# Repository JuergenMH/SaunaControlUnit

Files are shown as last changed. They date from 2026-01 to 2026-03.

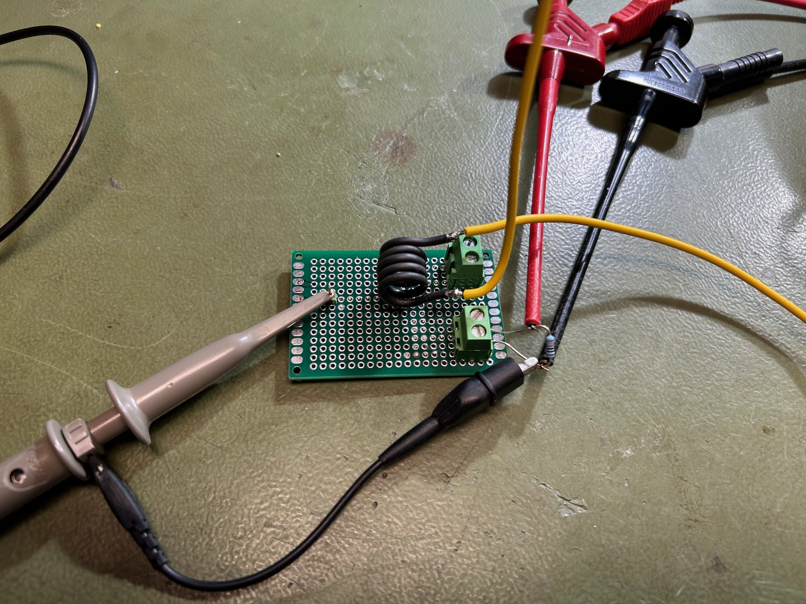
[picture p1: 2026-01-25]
Components/Home brew current sensor/Fotos/6. Coil #3 (in pperation).jpeg

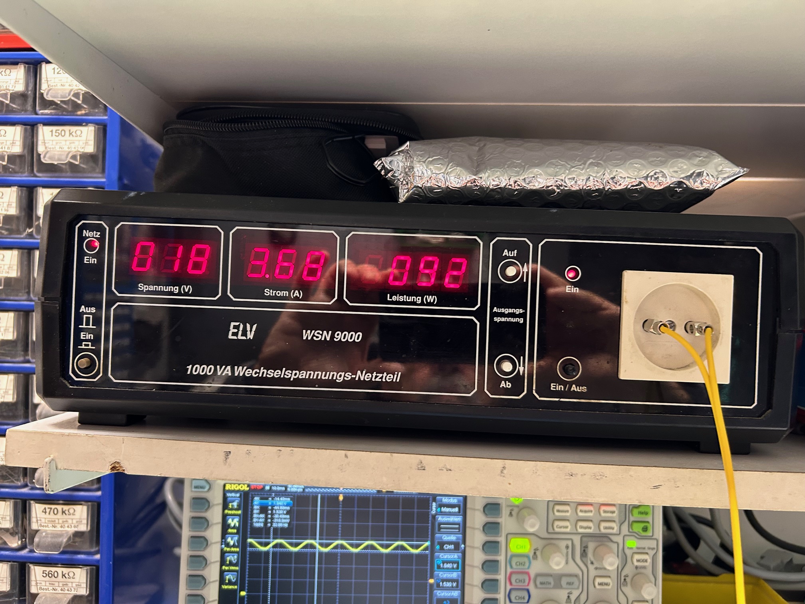
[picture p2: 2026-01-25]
Components/Home brew current sensor/Fotos/2. Power Supply Load Current (10, 20, .. 40V AC).jpeg

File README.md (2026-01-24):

# SaunaControlUnit
Control unit for sauna oven. Ensures comfort and safety.
Cheap control units are good for regualation and some basic safetey functions.
This project is designed to add some comfort and safety topics
- Enhanced safety by control internal power lines and oven function
- Enhanced comfort: Acceess via WLAN
- Two relay banks to ensure the system in case of one relay fails

Folders:
Components: Datasheets and information hardware component related
Documents:  Planning Documents
SaunaPCB:   KiCAD folder for schematic and PCB design files
Simulation: Folder for LTSpice simulation fils
Firmware:   Planned for firmware files, currently empty

Sorry, some documents are available in German only ;-)

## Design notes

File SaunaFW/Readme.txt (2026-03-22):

SW implementation startet with a home-brew cooperative multitasking.
This works fine, but some parts of the SW (e.g. LCD routines) are fare away from beeing "cooperative".
The latest version is stored in the zip file; still not fully implemented!

So I started a different concept. 
The idea is to use the already running FreeRTOS of the ESP32 module board to change the complete SW from cooperative to preemptive scheduling.
I start with an almost empty project and step by step I will move the already coded functions to the preemptive task scheduling.

Current state is:

FreeRTOS-Tasks
- TskMyIODrive.ino; Input driver modle is running and tested. 
- TskMyKTY.ino;     KTY module is running, results are wrong! => DEBUGGING required
- TskMyRelays.ino;  Relay control module, under construction

Other modules
- MyConfig.ino;     Configuration module as a standard arduino function (carry over from last version)
- MyEncoder.ino;    Encoder module ist running; completely interrupt driven; no FreeRTOS task!

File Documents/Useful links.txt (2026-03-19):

Basic information reagarding FreeRTOS and ESP32 (German):
https://wolles-elektronikkiste.de/freertos-mit-esp32-und-arduino-nutzen

Official FreeRTOS Documentaton:
https://www.freertos.org/Documentation/02-Kernel/04-API-references/01-Task-creation/00-TaskHandle

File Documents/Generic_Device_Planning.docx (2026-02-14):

# Bedienelemente

## Taster/Schalter

Netzschalter = > Ein- und Ausschalten der Steuerung („An“ oder „Aus“)

Modus-Taster => Wechsel zwischen den Betriebsarten „Aktiv“, „Standby“ und „Regelung an“
Kurzes Drücken = Wechsel zwischen „Aktiv“ und „Standby“
Langes Drücken = Wechsel zwischen „Aktiv“ und „Regelung an“
Kurzes Drücken im Modus „Regelung an“ = Quittierung Totmannschaltung

Licht-Taster => Licht ein- und ausschalten
Taster geht an Controller; Licht wird über Relais geschaltet
Bei jedem Drücken wechselt der Modus zwischen an und aus.

Drehencoder => Einstellen der Temperatur
Drücken des Tasters = Speichern als neue Default-Temperatur

Nur der Netzschalter schaltet 230V/AC, alle anderen Bedienelemente arbeiten mit Kleinspannung und gehen zur Elektronik.

## Leuchtdioden

Power LED (Grün) => Leuchtet, wenn Netzschalter in Position “An” ist.

Restliche Anzeigen gehen über das Display

## Anzeige (LCD 4 * 20)

Ausführung als hintergrundbeleuchtetes LCD mit Standard-Controller.

Benutzerdefinierte Symbole

- W = WLAN-Symbol
- °C
- Heizsymbol für Heizung an.

Es wird eine Version mit i²C => LCD Konverter verwendet.
Dazu benötigen wir nur 2 CPU-Leitungen.

## Grobkonzept Anzeigen

… ohne Anspruch auf Vollständigkeit

### Betriebsmodus „Aktiv“, warte auf Start (= Long press „Mode“)

1 | 4 | . | 0 | 2 | . | 2 | 0 | 2 | 6 | | 1 | 6 | : | 4 | 0
R | O | O | M | | : | 1 | 8 | °C | | | L | I | G | H | T | : | O | F | F
S | A | U | N | A | : | 7 | 8 | °C | | | D | O | O | R | | : | O | K
T | A | R | G | . | : | 8 | 0 | °C | | | S | T | A | T | E | : | R | D | Y

### Betriebsmodus „Regelung“

1 | 4 | . | 0 | 2 | . | 2 | 0 | 2 | 6 | | 1 | 6 | : | 4 | 0
R | O | O | M | | : | 1 | 8 | °C | | | L | I | G | H | T | : | O | F | F
S | A | U | N | A | : | 7 | 8 | °C | | | D | O | O | R | | : | O | K
T | A | R | G | . | : | 8 | 0 | °C | | | S | T | A | T | E | : | O | N | | Of

Of = Heizsymbol, wenn gerade geheizt wird.
Idee: Der Status blinkt, um den Betrieb etwas deutlicher anzuzeigen.

### Fehler: Tür offen

Wenn bei offener Tür versucht wird die Regelung zu starten:

1 | 4 | . | 0 | 2 | . | 2 | 0 | 2 | 6 | | 1 | 6 | : | 4 | 0
R | O | O | M | | : | 1 | 8 | °C | | | L | I | G | H | T | : | O | F | F
S | A | U | N | A | : | 7 | 8 | °C | | | D | O | O | R | | : | O | K
T | A | R | G | . | : | 8 | 0 | °C | | | S | T | A | T | E | : | D | O | O | R

Summe ertönt, Fehler wird für 2 Sekunden angezeigt, dann geht es zurück zum Zustand „Aktiv“

### Fehler: Übertemperatursicherung ausgelöst

1 | 4 | . | 0 | 2 | . | 2 | 0 | 2 | 6 | | 1 | 6 | : | 4 | 0
R | O | O | M | | : | 1 | 8 | °C | | | L | I | G | H | T | : | O | F | F
S | A | U | N | A | : | 7 | 8 | °C | | | D | O | O | R | | : | O | K
E | R | R | O | R | : | O | V | E | R | T | E | M | P | R | A | T | U | R | E

Summer ertönt, Regelung kann nicht mit Mode gestartet werden.

### Fehler: Sensorfehler Sauna

1 | 4 | . | 0 | 2 | . | 2 | 0 | 2 | 6 | | 1 | 6 | : | 4 | 0
R | O | O | M | | : | 1 | 8 | °C | | | L | I | G | H | T | : | O | F | F
S | A | U | N | A | : | ? | ? | °C | | | D | O | O | R | | : | O | K
E | R | R | O | R | : | S | E | N | S | O | R | | D | E | F | E | C | T

Summer ertönt, Regelung kann nicht mit Mode gestartet werden.

### Fehler: Sensorfehler Raumtemperatur

1 | 4 | . | 0 | 2 | . | 2 | 0 | 2 | 6 | | 1 | 6 | : | 4 | 0
R | O | O | M | | : | ? | ? | °C | | | L | I | G | H | T | : | O | F | F
S | A | U | N | A | : | 7 | 8 | °C | | | D | O | O | R | | : | O | K
T | A | R | G | . | : | 8 | 0 | °C | | | S | T | A | T | E | : | O | N | | Of

Summer ertönt kurz, Regelung kann aber gestartet werden. Fehleranzeige über ?? bei der Temperatur.

## Summer

Der Summer gibt ein kurzes Feedback in nachfolgenden Situationen:

- Speichern der eingestellten Temperatur (Drücken des Dreh-Encoders)
- Starten der Ofen-Regelung (Langes Drücken von „Mode“) Stoppen der Ofen-Regelung (Langes Drücken von „Mode“)
- Quittierung der „Totmannschaltung“ (Kurzes Drücken von Mode)

Ein langes Fehlersignal wird dann ausgegeben:

- Regelung soll gestartet werden, während die Tür offen ist
- Regelung soll gestartet werden, während ein Fehler vorliegt. (z.B. Überhitzungsschutz hat ausgelöst, sonstiger HW-Fehler)

# Powermodi

Netzschalter in Position „Aus“ => „Power off“, Elektronik inaktiv

Netzschalter in Position „An“ => „Power on“, Elektronik aktiv

Betriebsmodus „Standby“ => Alle Anzeigen aus, WLAN ist aktiv

Betriebsmodus „Aktiv“ => Display an, Regelung kann gestartet werden

Betriebsmodus „Regelung“ => Display an, Regelung wurde gestartet

Nach dem Einschalten des Netzschalters geht das System in den Zustand „An“ + „Aktiv“

Durch kurzes Drücken des Mode-Tasters wird zwischen „Aktiv“ und „Standby“ gewechselt.
Durch langes Drücken des Mode-Tasters wird die Regelung gestartet.

# Lichtsteuerung

Hinweis: Im Modus „Power off“ kann das Licht nicht eingeschaltet werden.
Um das Licht aktivieren zu können, muss das System im Modus „Power On“ sein.

Unabhängig vom Betriebsmodus (Aktiv/Standby) kann das Licht durch Druck auf den Licht-Taster ein- oder ausgeschaltet werden.

Wird die Regelung über den Start-Taster aktiviert, wird automatisch das Licht eingeschaltet.

# Grundlegende Bedienung im Saunabetrieb

## Allgemeine Nutzung

Sollte der Netzschalter in der Position „Aus“ stehen, ist der Schalter zuerst in die Position „An“ zu stellen. In diesem Fall wird nach dem Einschalten direkt der Betriebsmodus „Aktiv“ gewählt.

Ist der Netzschalter in der Position „An“ und der Betriebsmodus ist „Standby“, wird nach dem Drücken auf die Mode-Taster in den Modus „Aktiv“ gewechselt.

Anzeigt werden nun auf dem LCD:

- Status WLAN Verbindung (WLAN-SYMBOL)
- Uhrzeit (NTP, für spätere Erweiterungen)
- Aktuelle Temperatur in der Sauna und im Raum
- Zieltemperatur

Die Zieltemperatur ist die letzte eingestellte und gespeicherte Temperatur.
Sie kann über den Drehregler in den Grenzen von 40 bis 99°C eingestellt werden. Durch Drücken auf den Encoder-Knopf wird sie als nächste Default-Temperatur gespeichert.

Die Sauna heizt auf, nachdem der Mode-Knopf lange (3 Sekunden) gedrückt wurde.

Um die Ofenreglung abzuschalten, muss der Mode-Knopf wieder lange (3 Sekunden) gedrückt werden.
Hinweis: Kurzes Drücken des Mode-Knopfes setzt nur den Sicherheitstimer #1 zurück. Siehe dazu Kapitel „Sicherheitsfunktionen“.

Während des Betriebes kann jederzeit die Zieltemperatur verändert und auf Wunsch durch Drücken des Encoder-Knopfes auch gespeichert werden.

## Energie sparen (Software Funktionen)

1. Sollte das Gerät für mehr als drei Stunden aktiv sein, ohne dass der Regler gestartet wurde, schaltet das System automatisch in den Betriebsmodus „Standby“ zurück.
2. Wird zwei Stunden nach dem Drücken des Start-Tasters (Aufheizen) nicht die Saunatür geöffnet oder die Start-Taste am Regler gedrückt, wird die Ofenregelung wieder abgeschaltet.

Anmerkung: Die gesetzliche Regelung von max. 6 Stunden kommt nicht zur Anwendung, da die zweite Abschaltfunktion das weitestgehend mit abdeckt.

# Sicherheitsfunktionen

Das System weist mehrere Sicherheitsfunktionen auf:

1. Doppel-Relais (Hardware) Zwei in Reihe geschaltete Relais sollen sicherstellen, dass beim Kleben eines Relaiskontaktes keine Spannung dauerhaft am Ofen anliegt. Relais #1 schaltet, sobald die Ofenregelung gestartet wurde, dauerhaft an. Relais #2 realisiert dann die Regelung.
2. Übertemperaturabschaltung (Hardware) Wenn die Übertemperatursicherung anspricht, bekommen beide Relais keine Versorgungsspannung mehr und können nicht mehr aktiviert werden. Die Spannung wird von der Steuerung überwacht und es wird ein entsprechender Fehler ausgegeben. Ein Betrieb ist nicht möglich! Fehler zurücksetzen: Gerät reparieren und vollständigen Power-Zyklus
3. Sensorüberwachung Im Fall eines Kurzschlusses oder einer Unterbrechung der Sensorleitung wird ein entsprechender Fehler ausgegeben. Ein Betrieb der Steuerung ist dann nicht möglich. Fehler zurücksetzen: Sensor / Kabel reparieren und vollständigen Power-Zyklus
4. Tür-Schalter (Hardware) Die Ofenregelung kann nur bei geschlossener Saunatür gestartet werden. Wird versucht die Ofenregelung bei offener Tür zu starten, gibt es ein Signal vom Summer und es wird eine entsprechende Fehlermeldung ausgegeben. Fehler zurücksetzen: Tür schließen
5. Sicherheitstimer #1 (Software, Totmannschaltung) Ein 20-Minuten-Sicherheitstimer wird aktiviert, wenn die Temperatur mindestens 80% der Zieltemperatur erreicht hat und die Tür geöffnet wird. Danach wird der Sicherheitstimer bei jedem Öffnen der Tür zurückgesetzt und neu gestartet. Durch Drücken des Start-Tasters kann der Sicherheitstimer zusätzlich manuell zurückgesetzt werden. Das Zurücksetzen wird durch einen kurzen Signalton quittiert. Läuft der Timer ohne Quittierung ab, wird die Ofenregelung abgeschaltet, ein langer Signalton ausgegeben und eine Fehlermeldung angezeigt. Fehler zurücksetzen: Start Taster drücken
6. Sicherheitstimer #2 (Software, Saunabetrieb; gesetzliche Regelung) Nach sechs Stunden Saunabetrieb bei aktiver Ofenregelung wird diese automatisch abgeschaltet. Zusätzlich wird ein langer Signalton ausgegeben und eine Fehlermeldung angezeigt. Fehler zurücksetzen: System in den Betriebsmodus „Standby“ schalten

Ende des Dokuments

Konzept Saunasteuerung

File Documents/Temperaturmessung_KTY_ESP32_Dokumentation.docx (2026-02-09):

Temperaturmessung mit KTY-Sensor und ESP32

Technische Dokumentation

Autor: Juergen Eggeling
Datum: 09.02.2026

# Inhaltsverzeichnis

Hinweis: Das Inhaltsverzeichnis kann in Word über „Feld aktualisieren“ automatisch erzeugt werden.

# 1 Einleitung

Dieses Dokument beschreibt die Auslegung, Berechnung und Implementierung einer präzisen Temperaturmessung mit einem KTY-Temperatursensor (2000 Ω @ 25°C) an einem ESP32 unter Verwendung der Arduino-IDE.

# 2 Hardwareaufbau

Der KTY-Sensor ist zwischen ADC-Eingang und Masse geschaltet. Ein Pull-Up-Widerstand verbindet den ADC-Eingang mit der 3,3-Versorgung.

# 3 Blockschaltbild

+3.3V
|
[Pull-Up 2kΩ]
|
[ADC ESP32]
|
[KTY Sensor 2kΩ @25°C]
|
GND

# 4 Messprinzip

Der KTY-Sensor bildet mit dem Pull-Up-Widerstand einen Spannungsteiler. Die am ADC gemessene Spannung wird digitalisiert und anschließend in einen Sensorwiderstand umgerechnet.

# 5 Mathematisches Modell

Die Umrechnung von Widerstand in Temperatur erfolgt über ein kubisches Polynom nach der KTY-Normkennlinie. Die Inversion erfolgt mittels Newton-Iteration.

# 6 Kalibrieranleitung (1-Punkt)

1. Sensor und Referenzthermometer auf gleiche Temperatur bringen (z. B. 25°C).
2. Temperaturwert des ESP32 auslesen (T_mess).
3. Offset berechnen: T_OFFSET = T_ref – T_mess.
4. Offset im Code als Konstante eintragen oder im EEPROM speichern.
5. Offset bei jeder Messung addieren.

# 7 Fehlerbetrachtung

Ohne Kalibrierung ist mit einem typischen Gesamtfehler von ±0,8 bis ±1,2°C zu rechnen. Mit einer 1-Punkt-Kalibrierung reduziert sich der Fehler auf etwa ±0,4°C.

# 8 Optimierung des Pull-Up-Widerstands

Für den Messbereich 20–100°C ist ein Pull-Up-Widerstand von 2,2 kΩ bis 2,49 kΩ optimal, da er den Arbeitspunkt des Spannungsteilers in den linearen ADC-Bereich legt.

# 9 Arduino-Code

const int adcPin = 34;
const float Vref = 3.3;
const float pullup = 2000.0;
const float R25 = 2000.0;
const float A = 7.88e-3;
const float B = 1.94e-5;
const float C = 3.42e-8;
const float T_OFFSET = 0.0; // Kalibrierwert

float R_from_T(float T) {
float x = T - 25.0;
return R25 * (1 + A*x + B*x*x + C*x*x*x);
}

float dR_dT(float T) {
float x = T - 25.0;
return R25 * (A + 2*B*x + 3*C*x*x);
}

float T_from_R(float R) {
float T = 60.0;
for (int i = 0; i < 4; i++) {
T -= (R_from_T(T) - R) / dR_dT(T);
}
return T + T_OFFSET;
}

void setup() {
Serial.begin(115200);
analogReadResolution(12);
analogSetAttenuation(ADC_11db);
}

void loop() {
int adc = analogRead(adcPin);
float voltage = adc * (Vref / 4095.0);
float Rkty = pullup * (voltage / (Vref - voltage));
float temperature = T_from_R(Rkty);

Serial.print("Temperatur: ");
Serial.print(temperature, 2);
Serial.println(" °C");
delay(1000);
}

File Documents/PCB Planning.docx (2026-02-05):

# Trace width calculation

## Introduction

From the web:

- Tmax chosen = 80°C (to be checked)

Unfortunately, we have a lot of input parameters:

1. Max Power 6KW (my oven) or 9KW (for some headroom)
2. Trace width (2.x .. 3.x mm. >3mm is hard to route!)
3. Copper thickness (35 or 70µm, price?)

## Power sauna oven with 6KW (35µm)

Current per line: 6KW complete, 2KW per line
Iline (L1, L2, L3) = P / U = 2000/230 = 8,7A
Chosen for calculation 9A

Trace width: 3,0mm@35µm

Caclulator on: https://www.leiton.de/leiton-tools-leiterbahnerwaermung.html

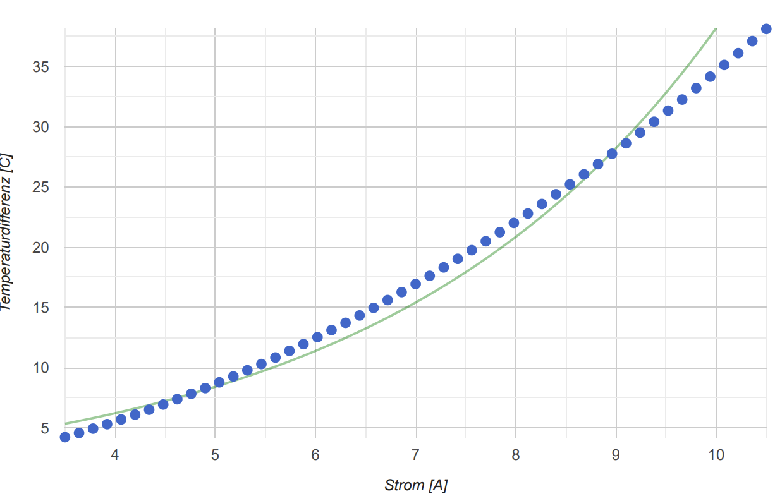
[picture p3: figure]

Delta T expected: + 28°C

Final trace temperature: 22°C room + 28°C heating = 50°C => OK

But 3mm is almost impossible to route under consideration of necessary distances.

## Power sauna oven width 9KW (35µm)

Current per line: 9KW complete, 3KW per line
Iline (L1, L2, L3) = P / U = 3000/230 = 13,04A
Chosen for calculation 13A

Trace width: 3,5mm@35µm

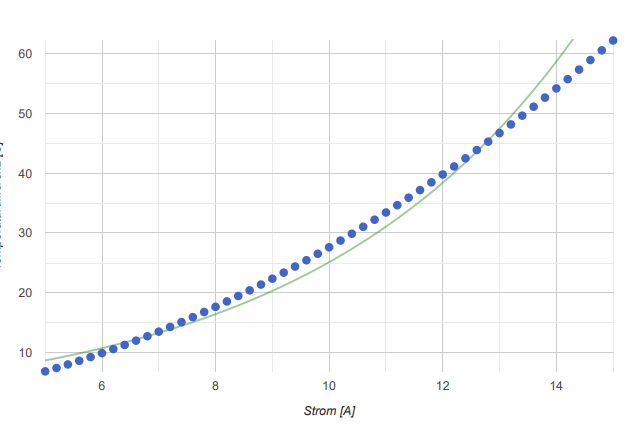
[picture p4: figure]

Delta T expected: + 47°C

Final trace temperature: 22°C room + 28°C heating = 69°C => OK

But 3.5mm is impossible to route under consideration of necessary distances.
=> Lets check 70µm on the next pages.
=> Assume: we try to reduce to 2mm trace width.

## Power sauna oven width 9KW (70µm)

Current per line: 9KW complete, 3KW per line
Iline (L1, L2, L3) = P / U = 3000/230 = 13,04A
Chosen for calculation 13A

Trace width: 2mm@70µm

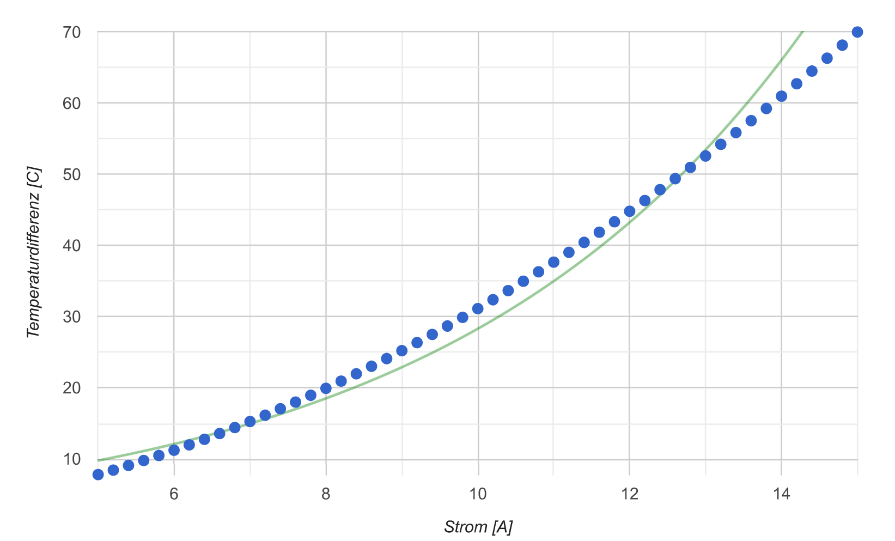
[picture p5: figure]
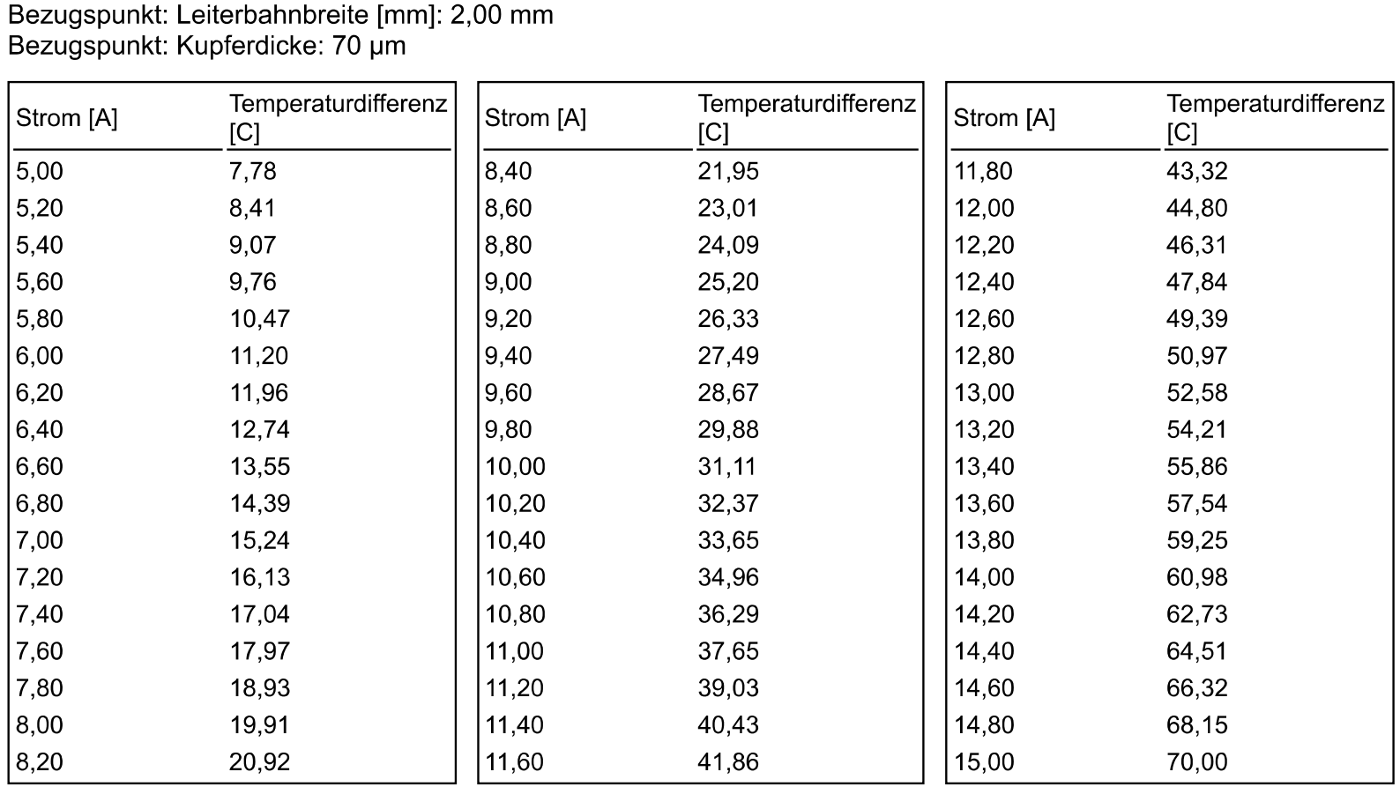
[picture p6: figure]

Delta T expected at 6KW: + 25°C

Final trace temperature: 22°C room + 25°C heating = 47°C => Good

Delta T expected at 9KW: + 53°C

Final trace temperature: 22°C room + 53°C heating = 75°C => Still OK

# Distance calculations

## Legal regulation

From common used legal regulations:

Use case 1: Phase Lx to Lx Functional isolation 2.5mm

Use case 2: Phase Lx to N or PE Base isolation 230V 3.0mm

Use case 3: Phase Lx to Ly Base isolation 400V 4.0mm

Use case 4: Phase Lx to ELV Double / enhanced isolation 6.0mm

With x, y = 1..3, ELV = Extrem low voltage e.g. 24V

## Usage in the design

Use case 1:

- Main switch
- Relay contacts

Use case 2:

- N.a.

Use case 3:

- Between different relays
- Between screw terminals

Use case 4:

- Voltage measurement components (near to Lx)
- Current measurement components (near to Lx)

# Addendum

## Table for temperature rise depending on current and trace width

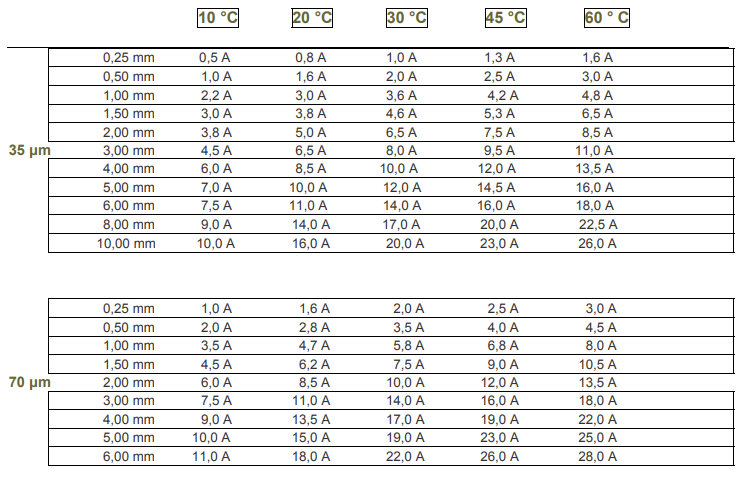
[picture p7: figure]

PCB Planning

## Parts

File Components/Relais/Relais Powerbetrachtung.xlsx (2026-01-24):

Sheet: Relais
Relais |  |  |  | Kontakte |  |  |  | Spule bei Nominalbetrieb (U rated) |  |  |  | Spule im Haltebetrieb |  |  | Worst case Betrachtung
Hersteller | Typ | Lieferant | Preis | max. Strom [A] | max. Spannung [VAC] | Schaltspiele | geschätzte Lebensdauer @ 20 Zyklen/Saunagang | Spannung [VDC] | Widerstand [Ohm] | Leistung [W] | Strom [A] | Spannung [VDC] | Strom [A] | Leistung [W] | Relais #1 [mA] | Relais #2 [mA] | Summe [mA] | Leistung [W]
Schrack/TE | RZ03-1A4-D024 | Reichelt | 1.85 | 16A | 250 | 50000 | 2500 | 24 | 1440 | 0.40 | 0.02 | 20 | 0.01 | 0.28 | 0.04 | 0.05 | 0.09 | 2.22
Omon | G2R-1A-E DC24 | Reichelt | 1.75 | 10A | 250 | 100000 | 5000 | 24 | 1100 | 0.52 | 0.02 | 20 | 0.02 | 0.36 | 0.05 | 0.07 | 0.12 | 2.88
Schrack | RP310024 Nachfolger RT314024 | Lager | 0 | 16A | 250 |  |  | 24 | 1100 | 0.52 | 0.02 | 20 | 0.02 | 0.40 | 0.06 | 0.07 | 0.13 | 3.01

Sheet: Leistungsbetrachtung
 | Spannung [V] | Strom [A] | Leistung [W]
Netzteil Spannung, Strom, Leistung | 24 | 0.23 | 5.52
Verbrauch für sechs Relais | 24 | 0.12 | 2.88
Rest für Schaltregler | 24 | 0.11 | 2.64
Für Elektronik bei 90%Wirkungsgrad | 5 | 0.48 | 2.38
Verbraucher ESP Maximalstrom |  | 0.40 |  | senden, kurzfristig
Verbraucher ESP Nominalstrom |  | 0.18 |  | empfangen, normal
=> Damit überhaupt ein LCD mit Hintergrundbeleuchtung betrieben werden kann, ist eine gute Entkopplung mit starken Elektrolytkondensatoren nötig!
Thema Stromversorgung ESP | https://arduino-hannover.de/2018/07/25/die-tuecken-der-esp32-stromversorgung/
Allgemeines zum ESP | https://wolles-elektronikkiste.de/esp32-mit-arduino-code-programmieren

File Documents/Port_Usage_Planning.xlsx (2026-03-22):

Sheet: Signal view
Signal view
Signal | Funktion | Pegel | Pin Name | Stift reihe | Pin Nummer
I_L1 | Analog input | 1,65V +/-x | ADC1_CH0 | 1 | 3
I_L2 | Analog input | 1,65V +/-x | ADC1_CH3 | 1 | 4
I_L3 | Analog input | 1,65V +/-x | ADC1_CH6 | 1 | 5
24VR Feedback | Analog input | 1,65V +/-x | ADC1_CH7 | 1 | 6
L1_Sense | Digital Input | 0-3,3V | GPIO32 | 1 | 7
L2_Sense | Digital Input | 0-3,3V | GPIO33 | 1 | 8
L3_Sense | Digital Input | 0-3,3V | GPIO25 | 1 | 9
Relais_1 | Digital Output | 0-3,3V | GPIO25 | 1 | 10
Relais_2 | Digital Output | 0-3,3V | GPIO27 | 1 | 11
Relais_3 | Digital Output | 0-3,3V | GPIO14 | 1 | 12
Light on/off button | Digital Input | 0-3,3V | GPIO22 | 1 | 13
Standby/On button | Digital Input | 0-3,3V | GPIO13 | 1 | 15
Door contact | Digital Input | 0-3,3V | GPIO15 | 2 | 17
LCD SCL | I2C Interface | 0-3,3V | GPIO22, SCL | 2 | 3
LCD SDA | I2C Interface | 0-3,3V | GPIO21, SDA | 2 | 6
LCD Backlight | Digital Output | 0-3,3V | GPIO19 | 2 | 8 | reserved
ENC_SWITCH | Digital Input | 0-3,3V | GPIO18 | 2 | 9
ENC_CLK | Digital Input | 0-3,3V | GPIO5 | 2 | 10
ENC_DT | Digital Input | 0-3,3V | GPIO17 | 2 | 11
ENC_VCC | Digital Output | 0-3,3V | GPIO16 | 2 | 12
Buzzer | Digital Output | 0-3,3V | GPIO2 | 2 | 24
KTY oven input | Analog input | 1,65V +/-x | ADC2_CH0 | 2 | 13
KTY room input | Analog input | 1,65V +/-x | ADC2_CH1 | 2 | 14

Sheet: ESP module view
ESP module connector view
Plannig J2 (left row) |  |  |  |  |  | Planning J3 (right row)
No. | Name | Type | Signal | Configuration | Chip function | No. | Name | Type | Signal | Configuration | Chip function
1 | 3V3 | Pwr | N.A. | N.A. | 3.3 V power supply | 1 | GND | Pwr | N.A. | N.A. | Ground
2 | EN | I | N.A. | N.A. | CHIP_PU, Reset | 2 | IO23 | I/O | Buzzer | Digital Output | GPIO23
3 | VP | I | I_L1 | Analog input | GPIO36, ADC1_CH0, S_VP | 3 | IO22 | I/O | LCD SCL | I2C Interface | GPIO22, SCL
4 | VN | I | I_L2 | Analog input | GPIO39, ADC1_CH3, S_VN | 4 | TX | I/O |  |  | GPIO1, U0TXD
5 | IO34 | I | I_L3 | Analog input | GPIO34, ADC1_CH6, VDET_1 | 5 | RX | I/O |  |  | GPIO3, U0RXD
6 | IO35 | I | 24VR Feedback | Analog input | GPIO35, ADC1_CH7, VDET_2 | 6 | IO21 | I/O | LCD SDA | I2C Interface | GPIO21, SDA
7 | IO32 | I/O | L1_Sense | Digital Input | GPIO32, ADC1_CH4, TOUCH_CH9, XTAL_32K_P | 7 | GND | Pwr | N.A. | N.A. | Ground
8 | IO33 | I/O | L2_Sense | Digital Input | GPIO33, ADC1_CH5, TOUCH_CH8, XTAL_32K_N | 8 | IO19 | I/O | Debug | Digital Output | GPIO19
9 | IO25 | I/O | L3_Sense | Digital Input | GPIO25, ADC1_CH8, DAC_1 | 9 | IO18 | I/O | ENC_Switch | Digital Input | GPIO18
10 | IO26 | I/O | Relais_1 | Digital PWM-Output | GPIO26, ADC2_CH9, DAC_2 | 10 | IO5 | I/O | ENC_CLK | Digital Input | GPIO5
11 | IO27 | I/O | Relais_2 | Digital PWM-Output | GPIO27, ADC2_CH7, TOUCH_CH7 | 11 | IO17 | I/O | ENC_DT | Digital Input | GPIO17
12 | IO14 | I/O | Relais_3 | Digital PWM-Output | GPIO14, ADC2_CH6, TOUCH_CH6, MTMS | 12 | IO16 | I/O | ENC_VCC | Digital Output | GPIO16
13 | IO12 | I/O | Light on/ff | Digital Input | GPIO12, ADC2_CH5, TOUCH_CH5, MTDI | 13 | IO4 | I/O | KTY oven input | Analog input | GPIO4, ADC2_CH0, TOUCH_CH0
14 | GND | Pwr | N.A. | N.A. | Ground | 14 | IO0 | I/O |  |  | GPIO0, ADC2_CH1, TOUCH_CH1, Boot
15 | IO13 | I/O | Mode | Digital Input | GPIO13, ADC2_CH4, TOUCH_CH4, MTCK | 16 | IO2 | I/O | KTY room input | Analog input | GPIO2, ADC2_CH2, TOUCH_CH2, !!!)
16 | D2 | I/O | Internally used for communication ESP and flash memory. Do not use! |  |  | 17 | IO15 | I/O | Door contact | Digital Input | GPIO15, ADC2_CH3, TOUCH_CH3, MTDO
17 | D3 | I/O |  |  |  | 17 | D1 | I/O | Internally used for communication ESP and flash memory. Do not use!
18 | CMD | I/O |  |  |  | 18 | D0 | I/O
19 | 5V | Pwr | N.A. | N.A. | 5 V power supply | 19 | CLK | I/O
https://docs.espressif.com/projects/esp-idf/en/v5.1/esp32/hw-reference/esp32/get-started-devkitc.html |  |  |  |  |  | !!!) If KTY not connected (Uin 3,3V) System does not enter Boot mode properly!
https://docs.sunfounder.com/projects/umsk/de/latest/03_esp32/esp32_lesson17_rotary_encoder.html

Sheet: Schematic LCD SPI
e

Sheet: KTY
https://wiki.hshl.de/wiki/index.php/PTC_Temperatursensor_KTY_81-210

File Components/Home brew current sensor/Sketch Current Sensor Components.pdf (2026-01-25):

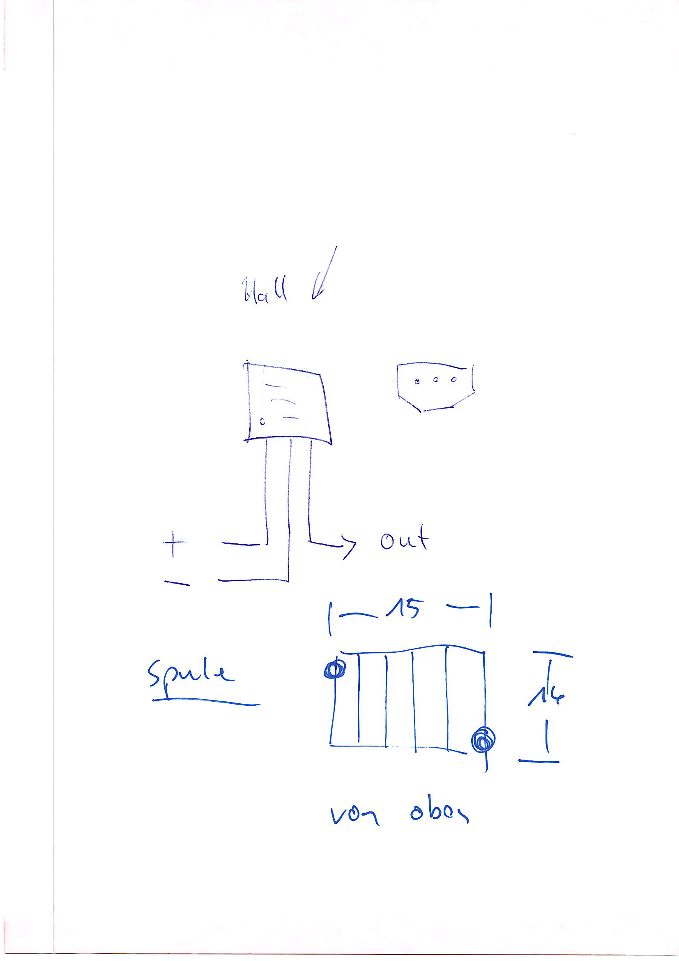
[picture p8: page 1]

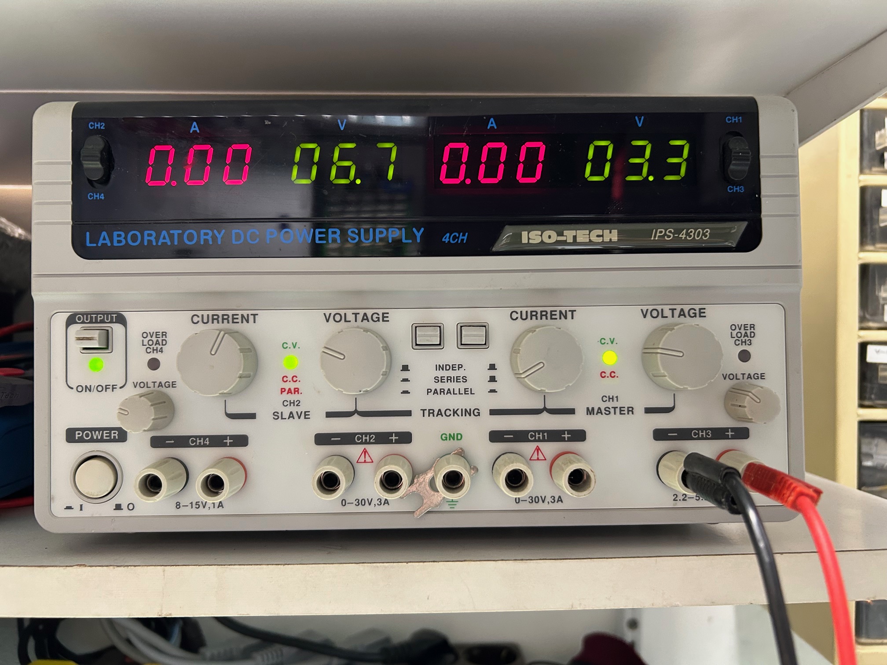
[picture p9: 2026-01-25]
Components/Home brew current sensor/Fotos/1. Power Supply Hall 3,3V.jpeg

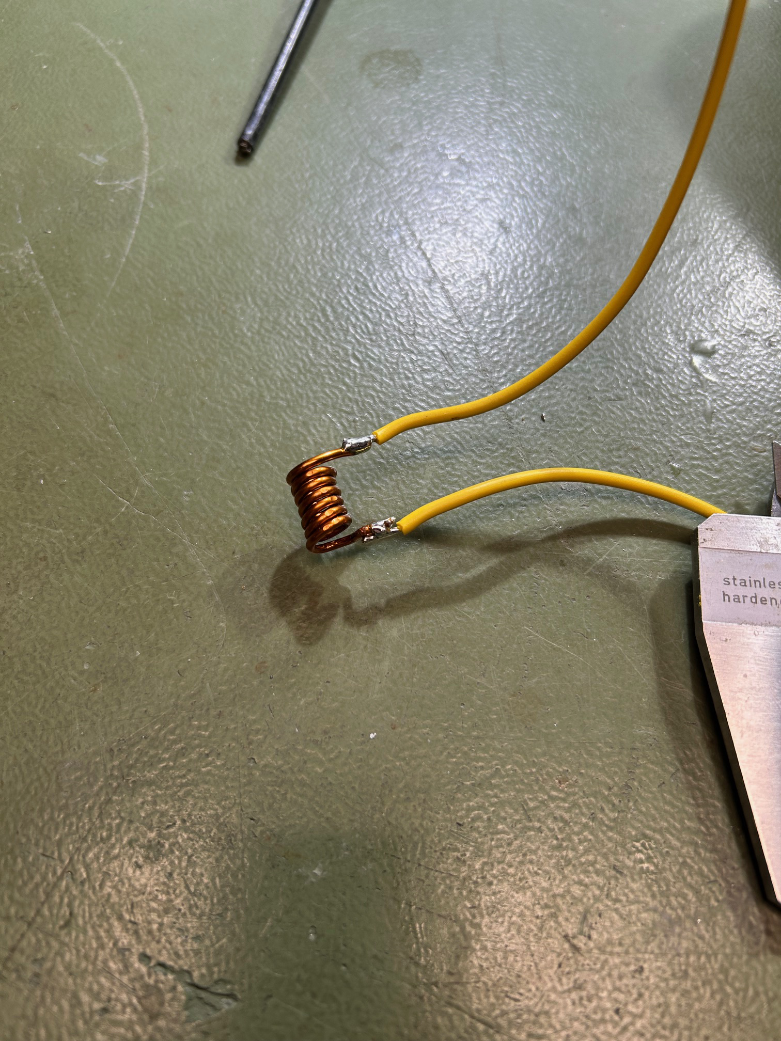
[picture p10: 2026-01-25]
Components/Home brew current sensor/Fotos/5. Coil #2 (on desk).jpeg

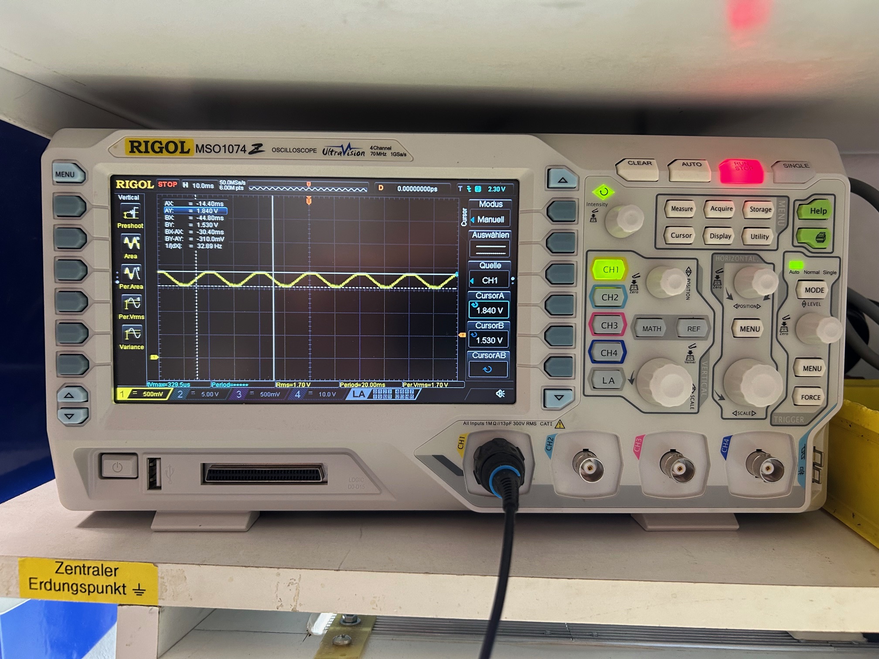
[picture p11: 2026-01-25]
Components/Home brew current sensor/Fotos/4. Hall Voltage Coil #1.jpeg

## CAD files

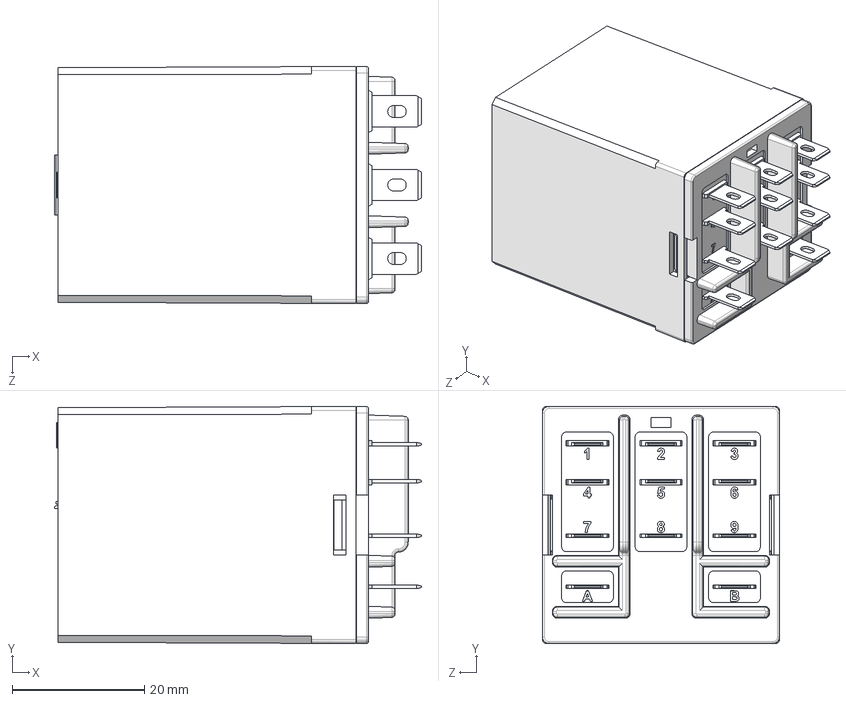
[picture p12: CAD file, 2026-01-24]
Components/Relais/c_rmx72xxx--_3d.stp
55.4 x 35.8 x 35.8 mm

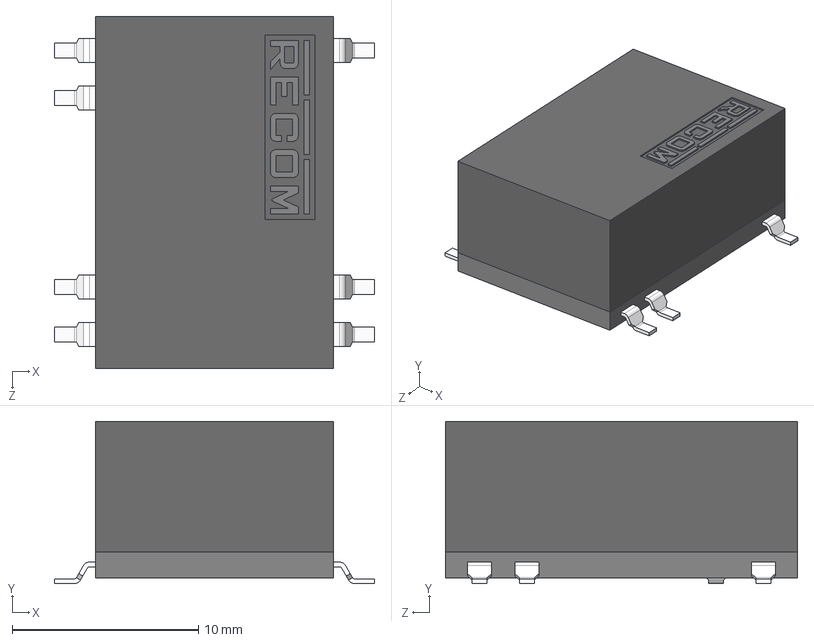
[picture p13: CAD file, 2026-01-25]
SaunaPCB/RSH2-2405S_H3-R.step
17.2 x 8.70 x 18.9 mm

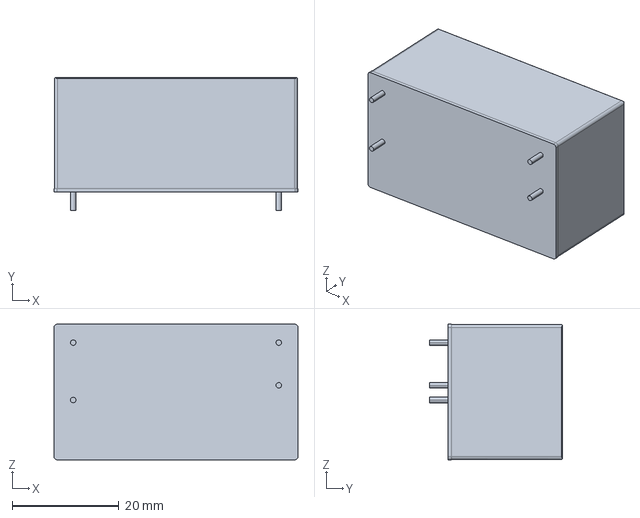
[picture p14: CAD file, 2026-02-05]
SaunaPCB/Step/power_supply_irm-05-24.stp
45.7 x 25.0 x 25.4 mm

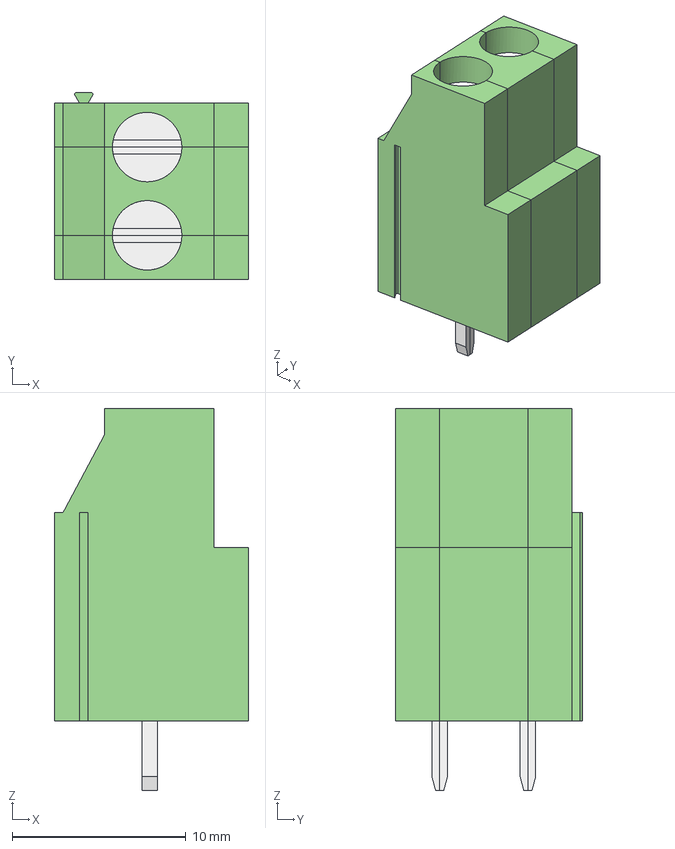
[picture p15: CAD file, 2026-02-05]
SaunaPCB/Step/KL_2-pol_RM5.stp
11.2 x 10.8 x 22.0 mm
MRT5P5.08_SX
MRT5P5.08_CNT
MRT5P5.08_DX

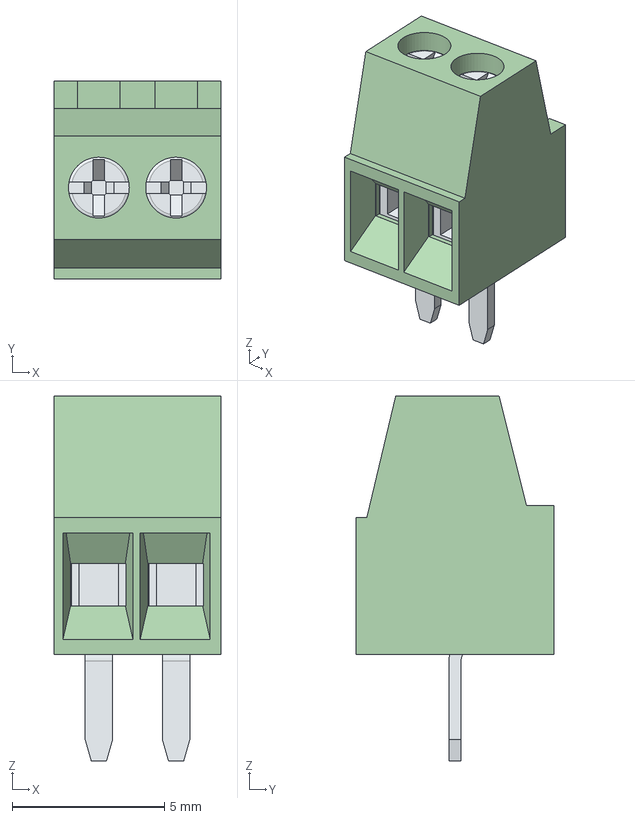
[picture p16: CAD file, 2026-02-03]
SaunaPCB/Step/KL2_RM_7.62_691210910002 (rev1).stp
5.48 x 6.50 x 12.0 mm
6912109100xx_CAGE x 2
6912109100xx_PIN x 2
6912109100xx_VIS x 2

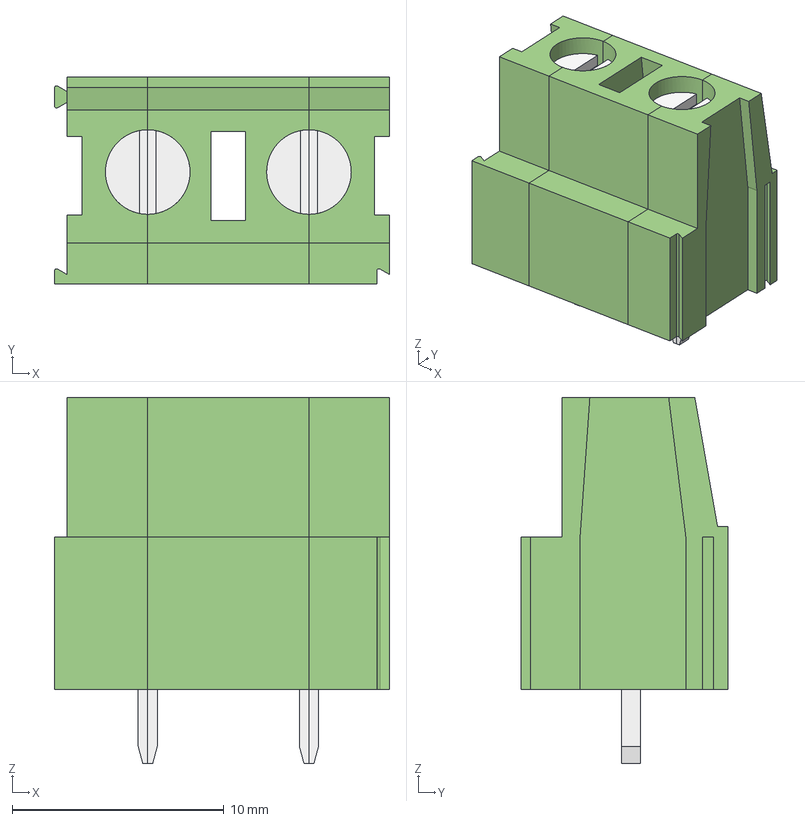
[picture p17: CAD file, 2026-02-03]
SaunaPCB/Step/KL2_RM_5.08_691216410002 (rev1).stp
15.8 x 9.80 x 17.3 mm
CLL7.62_DX
CLL7.62_CNT
CLL7.62_SX

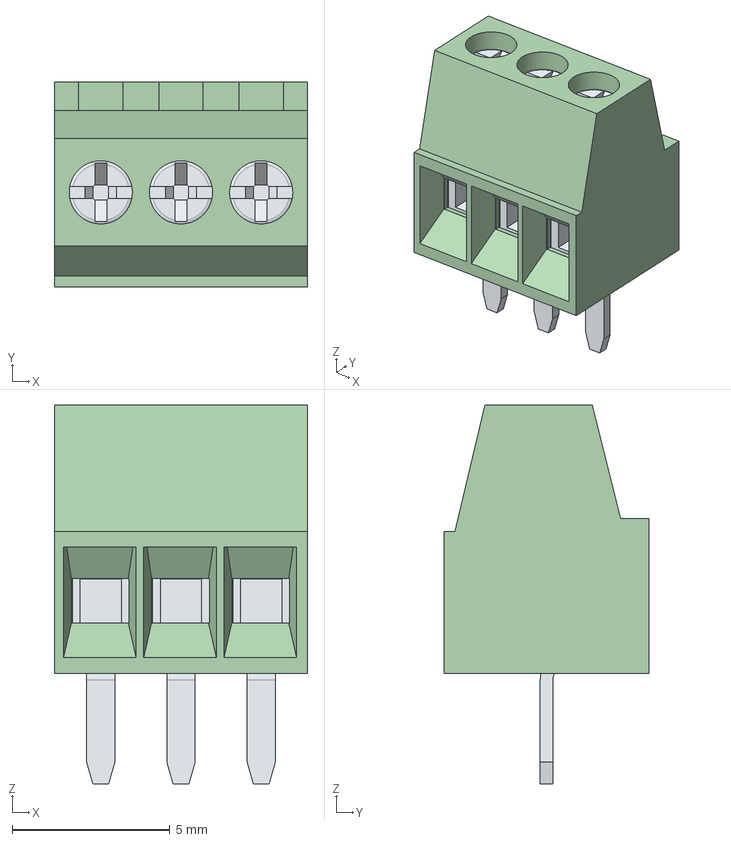
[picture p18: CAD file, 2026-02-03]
SaunaPCB/Step/KL3_RM_7.62_691210910003 (rev1).stp
8.02 x 6.50 x 12.0 mm
6912109100xx_CAGE x 3
6912109100xx_PIN x 3
6912109100xx_VIS x 3

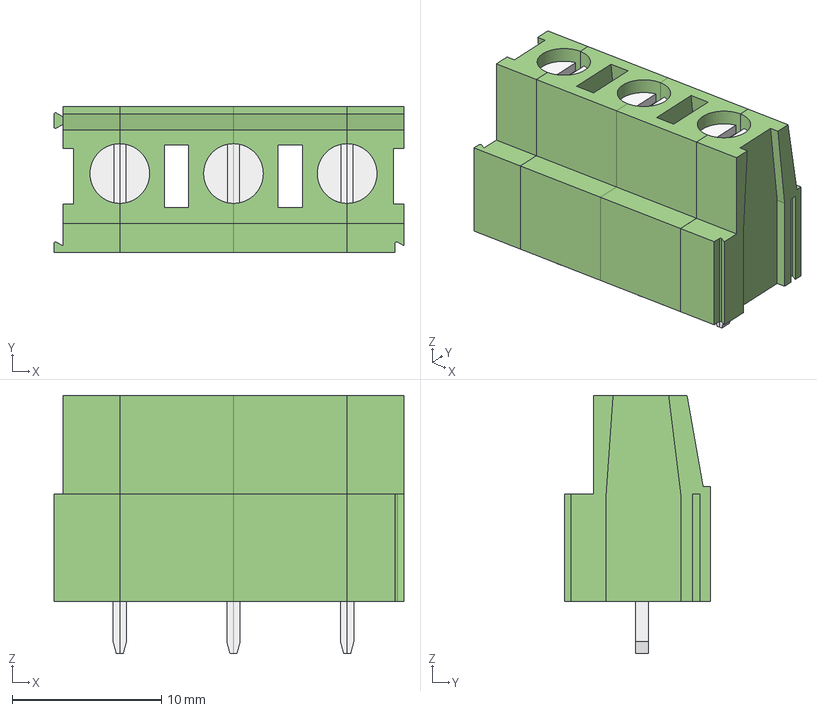
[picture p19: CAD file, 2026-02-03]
SaunaPCB/Step/KL3_RM_5.08_691216410003 (rev1).stp
23.5 x 9.80 x 17.3 mm
CLL7.62_DX
CLL7.62_CNT x 2
CLL7.62_SX

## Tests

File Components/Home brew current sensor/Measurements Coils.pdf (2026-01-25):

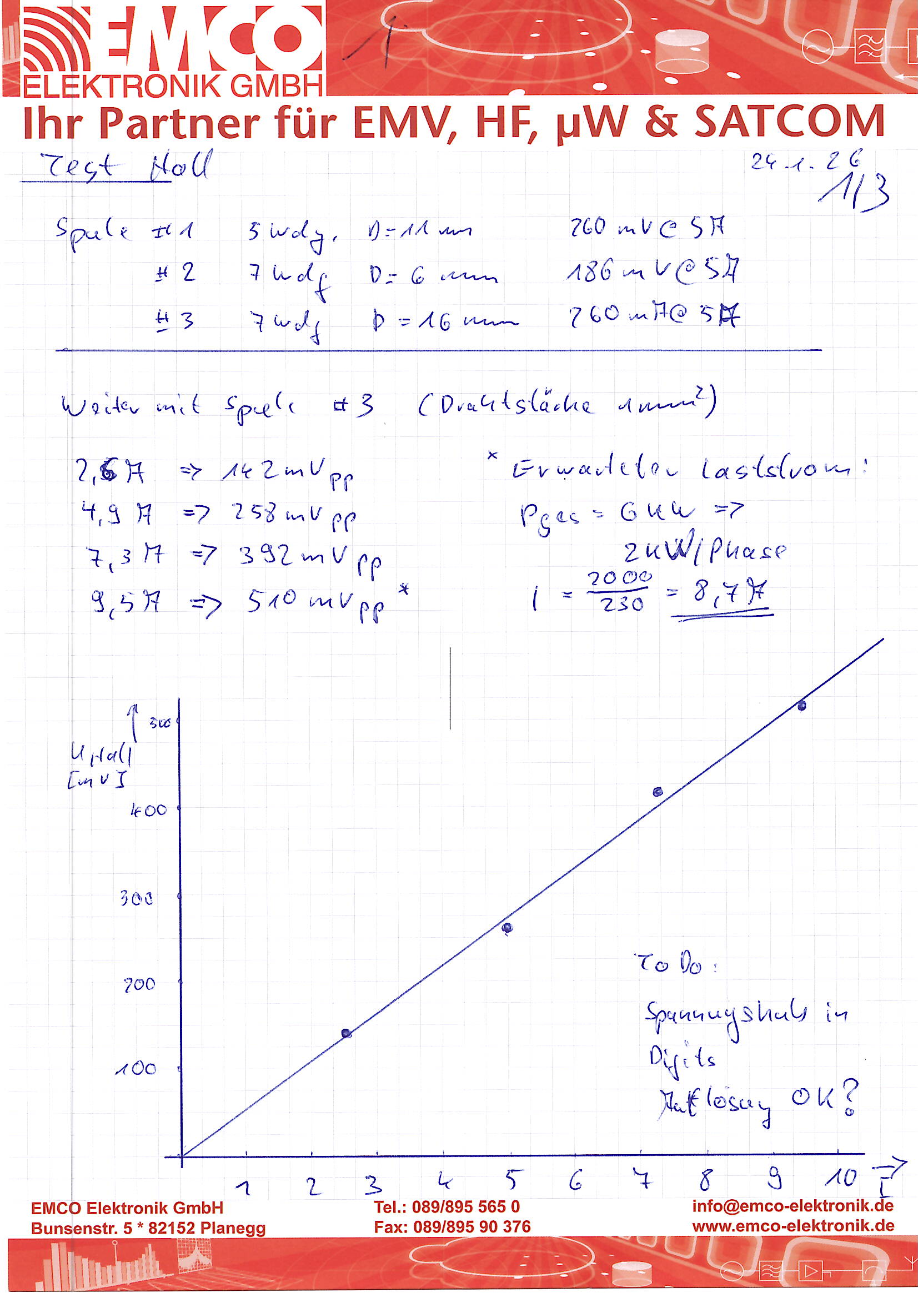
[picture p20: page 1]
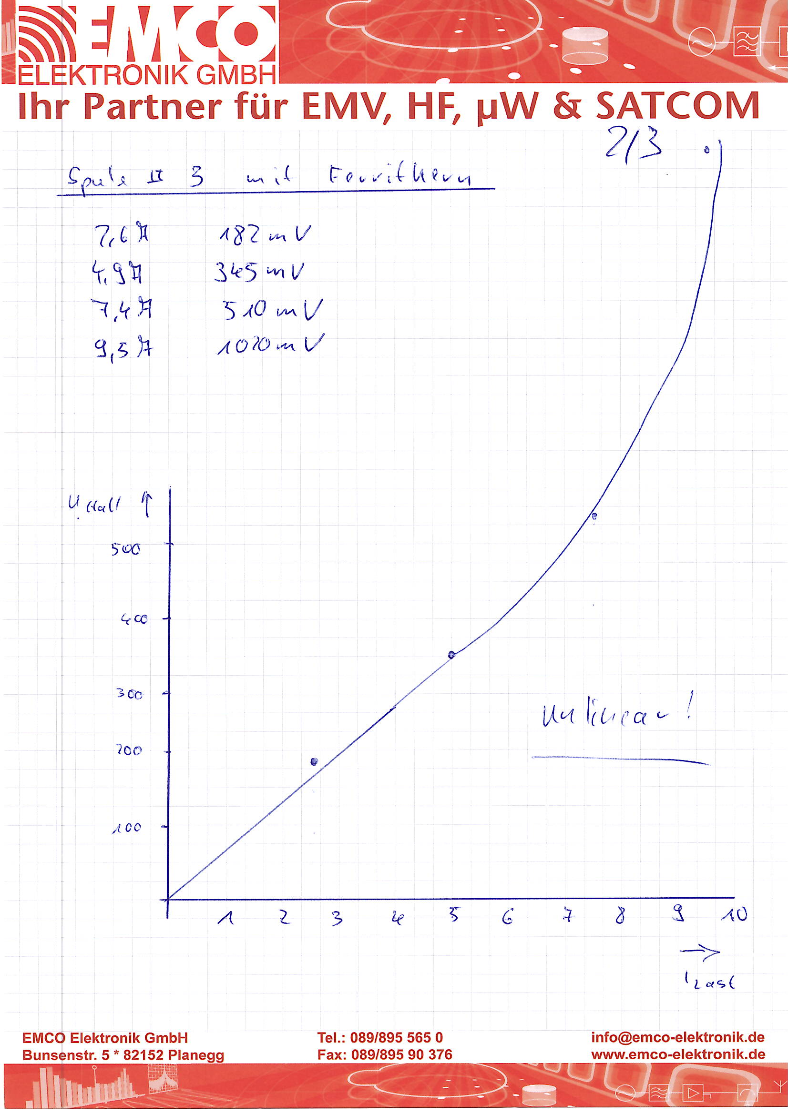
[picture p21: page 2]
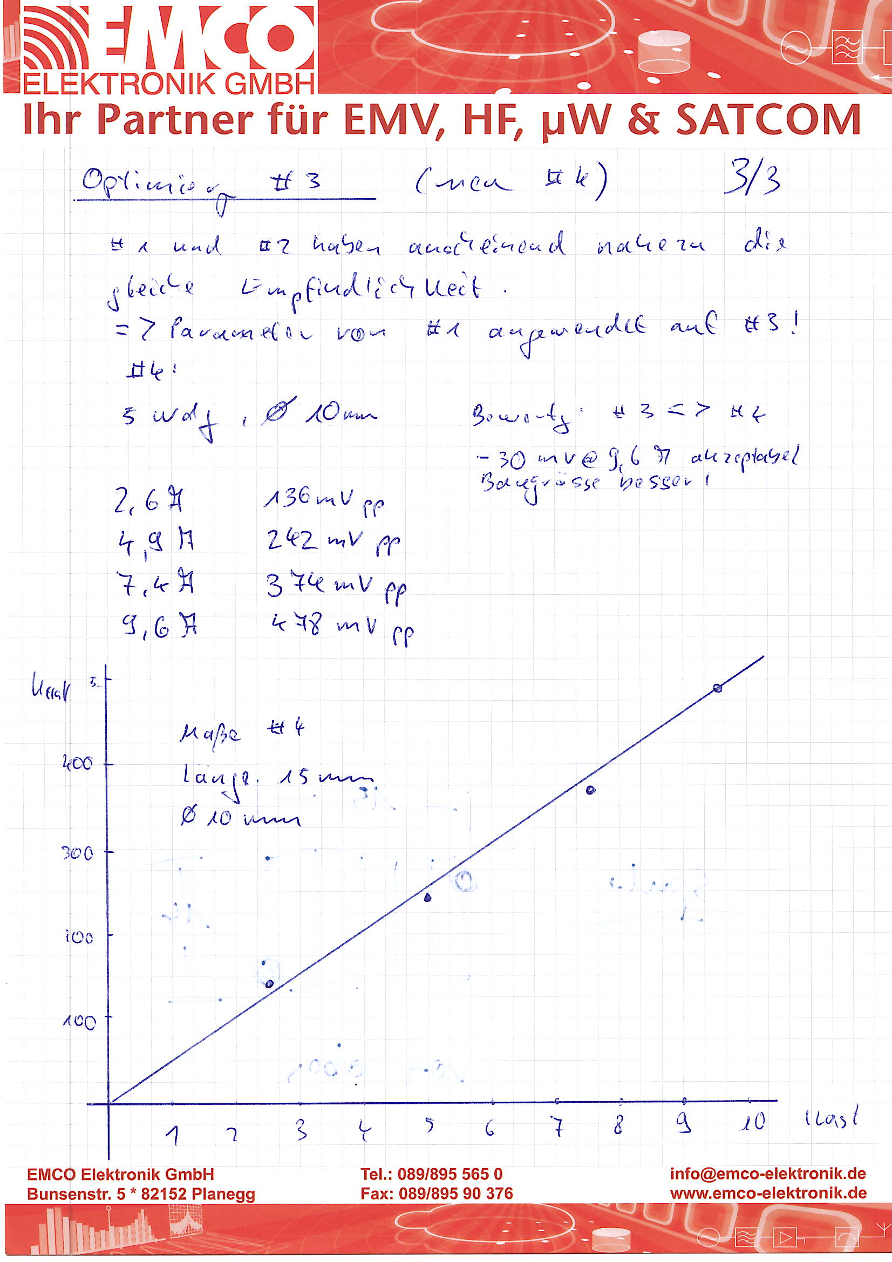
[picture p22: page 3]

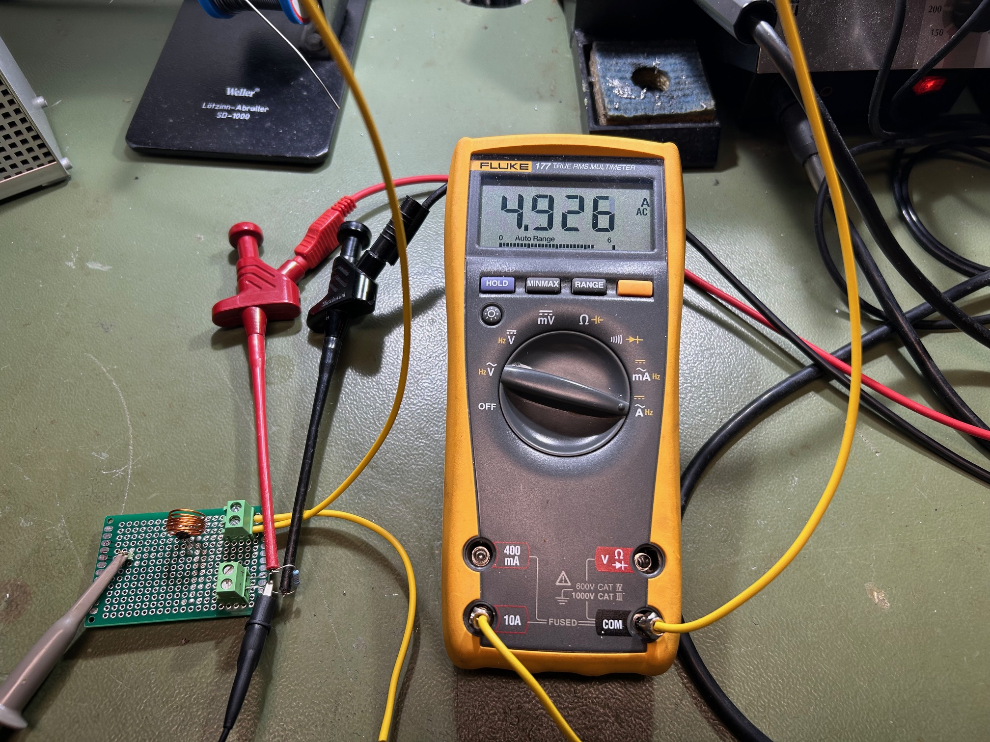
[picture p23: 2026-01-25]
Components/Home brew current sensor/Fotos/3. Current Measure Coil #1.jpeg

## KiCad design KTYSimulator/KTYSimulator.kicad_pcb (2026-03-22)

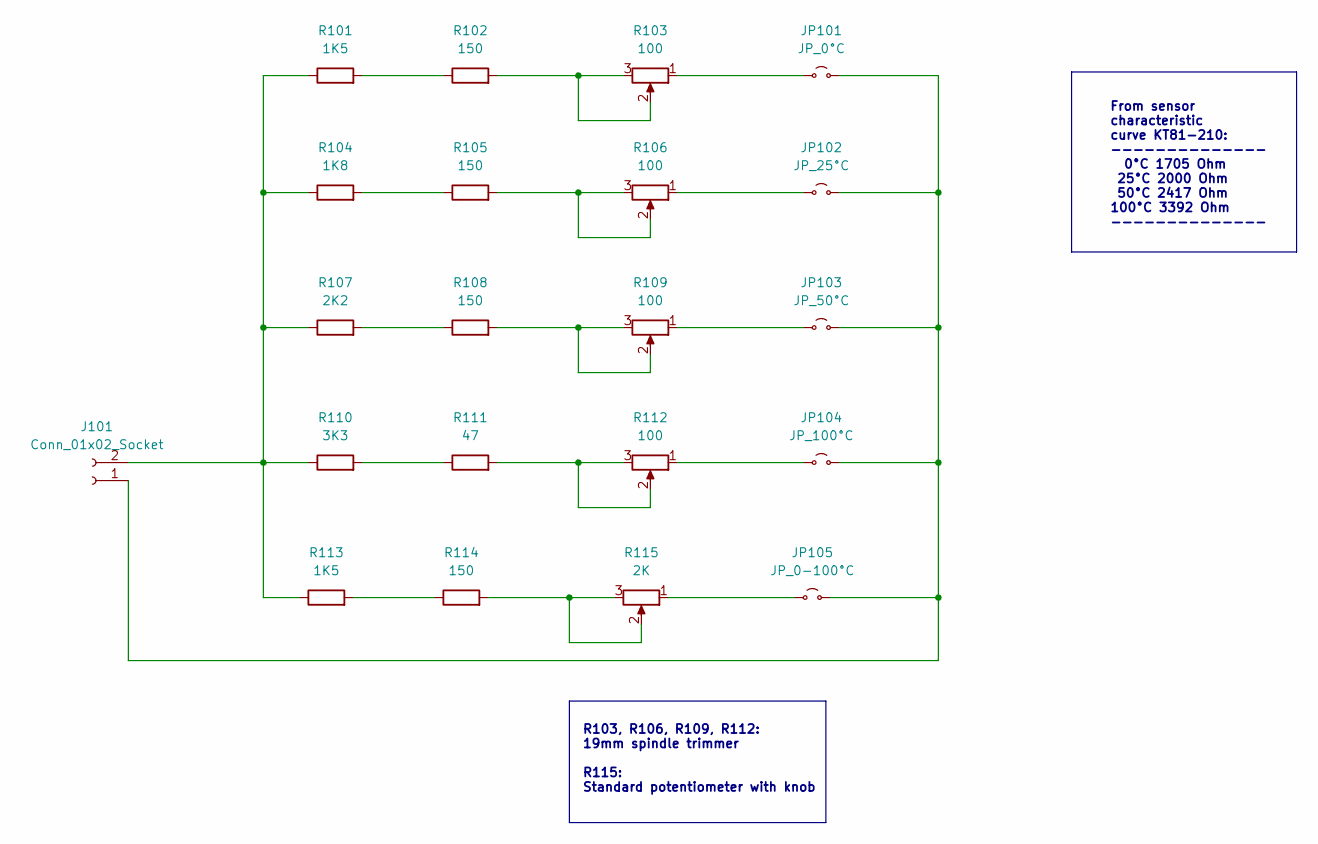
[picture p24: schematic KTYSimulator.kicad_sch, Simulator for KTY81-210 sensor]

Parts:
J101: Conn_01x02_Socket; PinHeader_1x02_P2.54mm_Vertical
JP101: JP_0°C; PinHeader_1x02_P2.54mm_Vertical
JP102: JP_25°C; PinHeader_1x02_P2.54mm_Vertical
JP103: JP_50°C; PinHeader_1x02_P2.54mm_Vertical
JP104: JP_100°C; PinHeader_1x02_P2.54mm_Vertical
JP105: JP_0-100°C; PinHeader_1x02_P2.54mm_Vertical
R101, R113: 1K5; R_Axial_DIN0207_L6.3mm_D2.5mm_P10.16mm_Horizontal
R102, R105, R108, R114: 150; R_Axial_DIN0207_L6.3mm_D2.5mm_P10.16mm_Horizontal
R103, R106, R109, R112: 100; Potentiometer_Bourns_3005_Horizontal
R104: 1K8; R_Axial_DIN0207_L6.3mm_D2.5mm_P10.16mm_Horizontal
R107: 2K2; R_Axial_DIN0207_L6.3mm_D2.5mm_P10.16mm_Horizontal
R110: 3K3; R_Axial_DIN0207_L6.3mm_D2.5mm_P10.16mm_Horizontal
R111: 47; R_Axial_DIN0207_L6.3mm_D2.5mm_P10.16mm_Horizontal
R115: 2K; Potentiometer_Alps_RK09Y11_Single_Horizontal

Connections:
unnamed: J101.1, JP101.2 (B), JP102.2 (B), JP103.2 (B), JP104.2 (B), JP105.2 (B)
unnamed: J101.2, R101.1, R104.1, R107.1, R110.1, R113.1
unnamed: JP101.1 (A), R103.1
unnamed: JP102.1 (A), R106.1
unnamed: JP103.1 (A), R109.1
unnamed: JP104.1 (A), R112.1
unnamed: JP105.1 (A), R115.1
unnamed: R101.2, R102.1
unnamed: R102.2, R103.2, R103.3
unnamed: R104.2, R105.1
unnamed: R105.2, R106.2, R106.3
unnamed: R107.2, R108.1
unnamed: R108.2, R109.2, R109.3
unnamed: R110.2, R111.1
unnamed: R111.2, R112.2, R112.3
unnamed: R113.2, R114.1
unnamed: R114.2, R115.2, R115.3

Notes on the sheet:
From sensor characteristic curve KT81-210: -------------- 0°C 1705 Ohm 25°C 2000 Ohm 50°C 2417 Ohm 100°C 3392 Ohm --------------
R103, R106, R109, R112: 19mm spindle trimmer R115: Standard potentiometer with knob

Board: 2 copper layers, 21 parts (0 on the bottom side), 17 nets, no tracks yet.

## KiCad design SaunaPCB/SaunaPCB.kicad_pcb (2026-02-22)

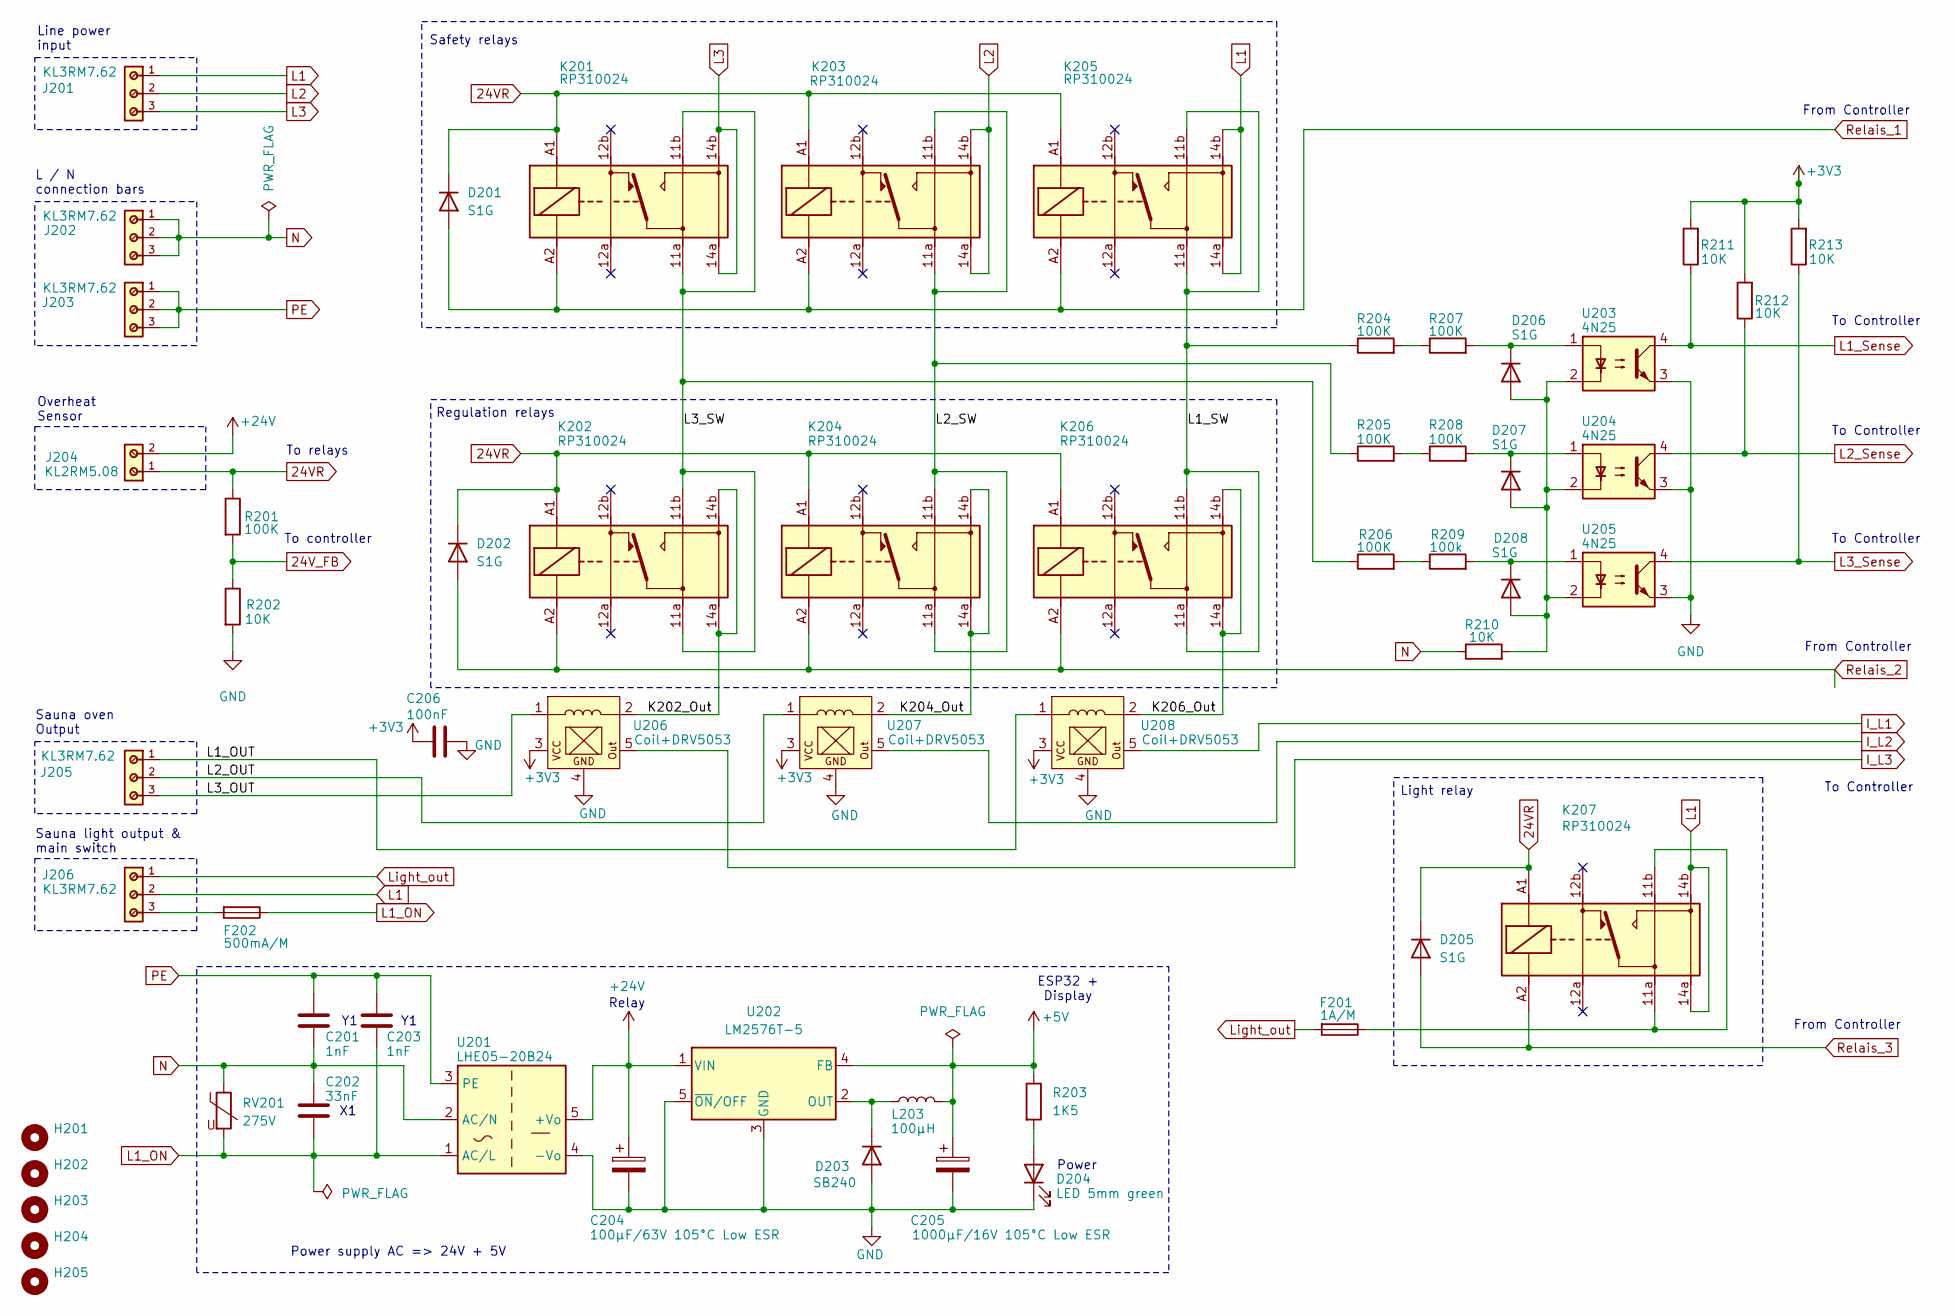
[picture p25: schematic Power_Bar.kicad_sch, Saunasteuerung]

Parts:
C201, C203: 1nF; C_Axial_L12.0mm_D6.5mm_P15.00mm_Horizontal
C202: 33nF; C_Axial_L12.0mm_D6.5mm_P15.00mm_Horizontal
C204: 100µF/63V 105°C Low ESR; CP_Radial_D10.0mm_P5.00mm
C205: 1000µF/16V 105°C Low ESR; CP_Radial_D10.0mm_P5.00mm
C206: 100nF; C_0805_2012Metric
D201, D202, D205, D206, D207, D208: S1G; D_SMA_Handsoldering
D203: SB240; D_A-405_P10.16mm_Horizontal
D204: LED 5mm green; B2B-ZR
F201: 1A/M; Fuseholder_Cylinder-5x20mm_Schurter_0031_8201_Horizontal_Op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
F202: 500mA/M; Fuseholder_Cylinder-5x20mm_Schurter_0031_8201_Horizontal_Op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
H201, H202, H203, H204, H205: MountingHole; MountingHole_3.2mm_M3_DIN965
J201, J202, J203, J205, J206: KL3RM7.62; Terminal_Block_3_RM7.62
J204: KL2RM5.08; Terminal_Block_2_RM5.08
K201, K202, K203, K204, K205, K206, K207: RP310024; Standard_Relay_double Pins
L203: 100µH; L_Radial_D7.5mm_P5.00mm_Fastron_07P
R201, R204, R205, R206, R207, R208: 100K; R_1206_3216Metric
R202, R210, R211, R212, R213: 10K; R_1206_3216Metric
R203: 1K5; R_1206_3216Metric
R209: 100k; R_1206_3216Metric
RV201: 275V; RV_Disc_D12mm_W4.2mm_P7.5mm
U201: LHE05-20B24
U202: LM2576T-5; TO-220-5_Vertical
U203, U204, U205: 4N25; DIP-4_W7.62mm
U206, U207, U208: Coil+DRV5053; Current_Coil_19X14_w_Hall

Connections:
24VR: D201.1 (K), D202.1 (K), D205.1 (K), J204.1, K201.A1, K202.A1, K203.A1, K204.A1, K205.A1, K206.A1, K207.A1, R201.1; also elsewhere on the board
24V_FB: R201.2, R202.1; also elsewhere on the board
+3V3: C206.1, R211.2, R212.2, R213.2, U206.3, U207.3, U208.3; also elsewhere on the board
+5V: C205.1, L203.2, R203.1, U202.4 (FB); also elsewhere on the board
+24V: C204.1, J204.2, U201.5 (+Vo), U202.1 (VIN)
/Power distribution part/K202_Out: K202.14a, K202.14b, U206.2
/Power distribution part/K204_Out: K204.14a, K204.14b, U207.2
/Power distribution part/K206_Out: K206.14a, K206.14b, U208.2
/Power distribution part/L1_OUT: J205.1, U208.1
/Power distribution part/L1_SW: K205.11a, K205.11b, K206.11a, K206.11b, R204.1
/Power distribution part/L2_OUT: J205.2, U207.1
/Power distribution part/L2_SW: K203.11a, K203.11b, K204.11a, K204.11b, R205.1
/Power distribution part/L3_OUT: J205.3, U206.1
/Power distribution part/L3_SW: K201.11a, K201.11b, K202.11a, K202.11b, R206.1
GND: C204.2, C205.2, C206.2, D203.2 (A), D204.1 (K), R202.2, U201.4 (-Vo), U202.3 (GND), U202.5 (~ON/OFF), U203.3, U204.3, U205.3, U206.4, U207.4, U208.4; also elsewhere on the board
I_L1: U208.5; also elsewhere on the board
I_L2: U207.5; also elsewhere on the board
I_L3: U206.5; also elsewhere on the board
L1: J201.1, J206.2, K205.14a, K205.14b, K207.14a, K207.14b
L1_ON: C202.2, C203.2, F202.1, RV201.2, U201.1 (AC/L)
L1_Sense: R211.1, U203.4; also elsewhere on the board
L2: J201.2, K203.14a, K203.14b
L2_Sense: R212.1, U204.4; also elsewhere on the board
L3: J201.3, K201.14a, K201.14b
L3_Sense: R213.1, U205.4; also elsewhere on the board
Light_out: F201.2, J206.1
N: C201.2, C202.1, J202.1, J202.2, J202.3, R210.1, RV201.1, U201.2 (AC/N)
unnamed: D203.1 (K), L203.1, U202.2 (OUT)
unnamed: D204.2 (A), R203.2
unnamed: D206.2 (A), D207.2 (A), D208.2 (A), R210.2, U203.2, U204.2, U205.2
unnamed: D206.1 (K), R207.2, U203.1
unnamed: D207.1 (K), R208.2, U204.1
unnamed: D208.1 (K), R209.2, U205.1
unnamed: F201.1, K207.11a, K207.11b
unnamed: F202.2, J206.3
unnamed: R204.2, R207.1
unnamed: R205.2, R208.1
unnamed: R206.2, R209.1
PE: C201.1, C203.1, J203.1, J203.2, J203.3, U201.3 (PE)
Relais_1: D201.2 (A), K201.A2, K203.A2, K205.A2; also elsewhere on the board
Relais_2: D202.2 (A), K202.A2, K204.A2, K206.A2; also elsewhere on the board
Relais_3: D205.2 (A), K207.A2; also elsewhere on the board

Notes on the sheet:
From Controller
Power supply AC => 24V + 5V
Regulation relays
L / N connection bars
To Controller
Light relay
Overheat Sensor
Sauna oven Output
To relays
To controller
Safety relays
Line power input
Sauna light output & main switch
Power
ESP32 + Display
Relay

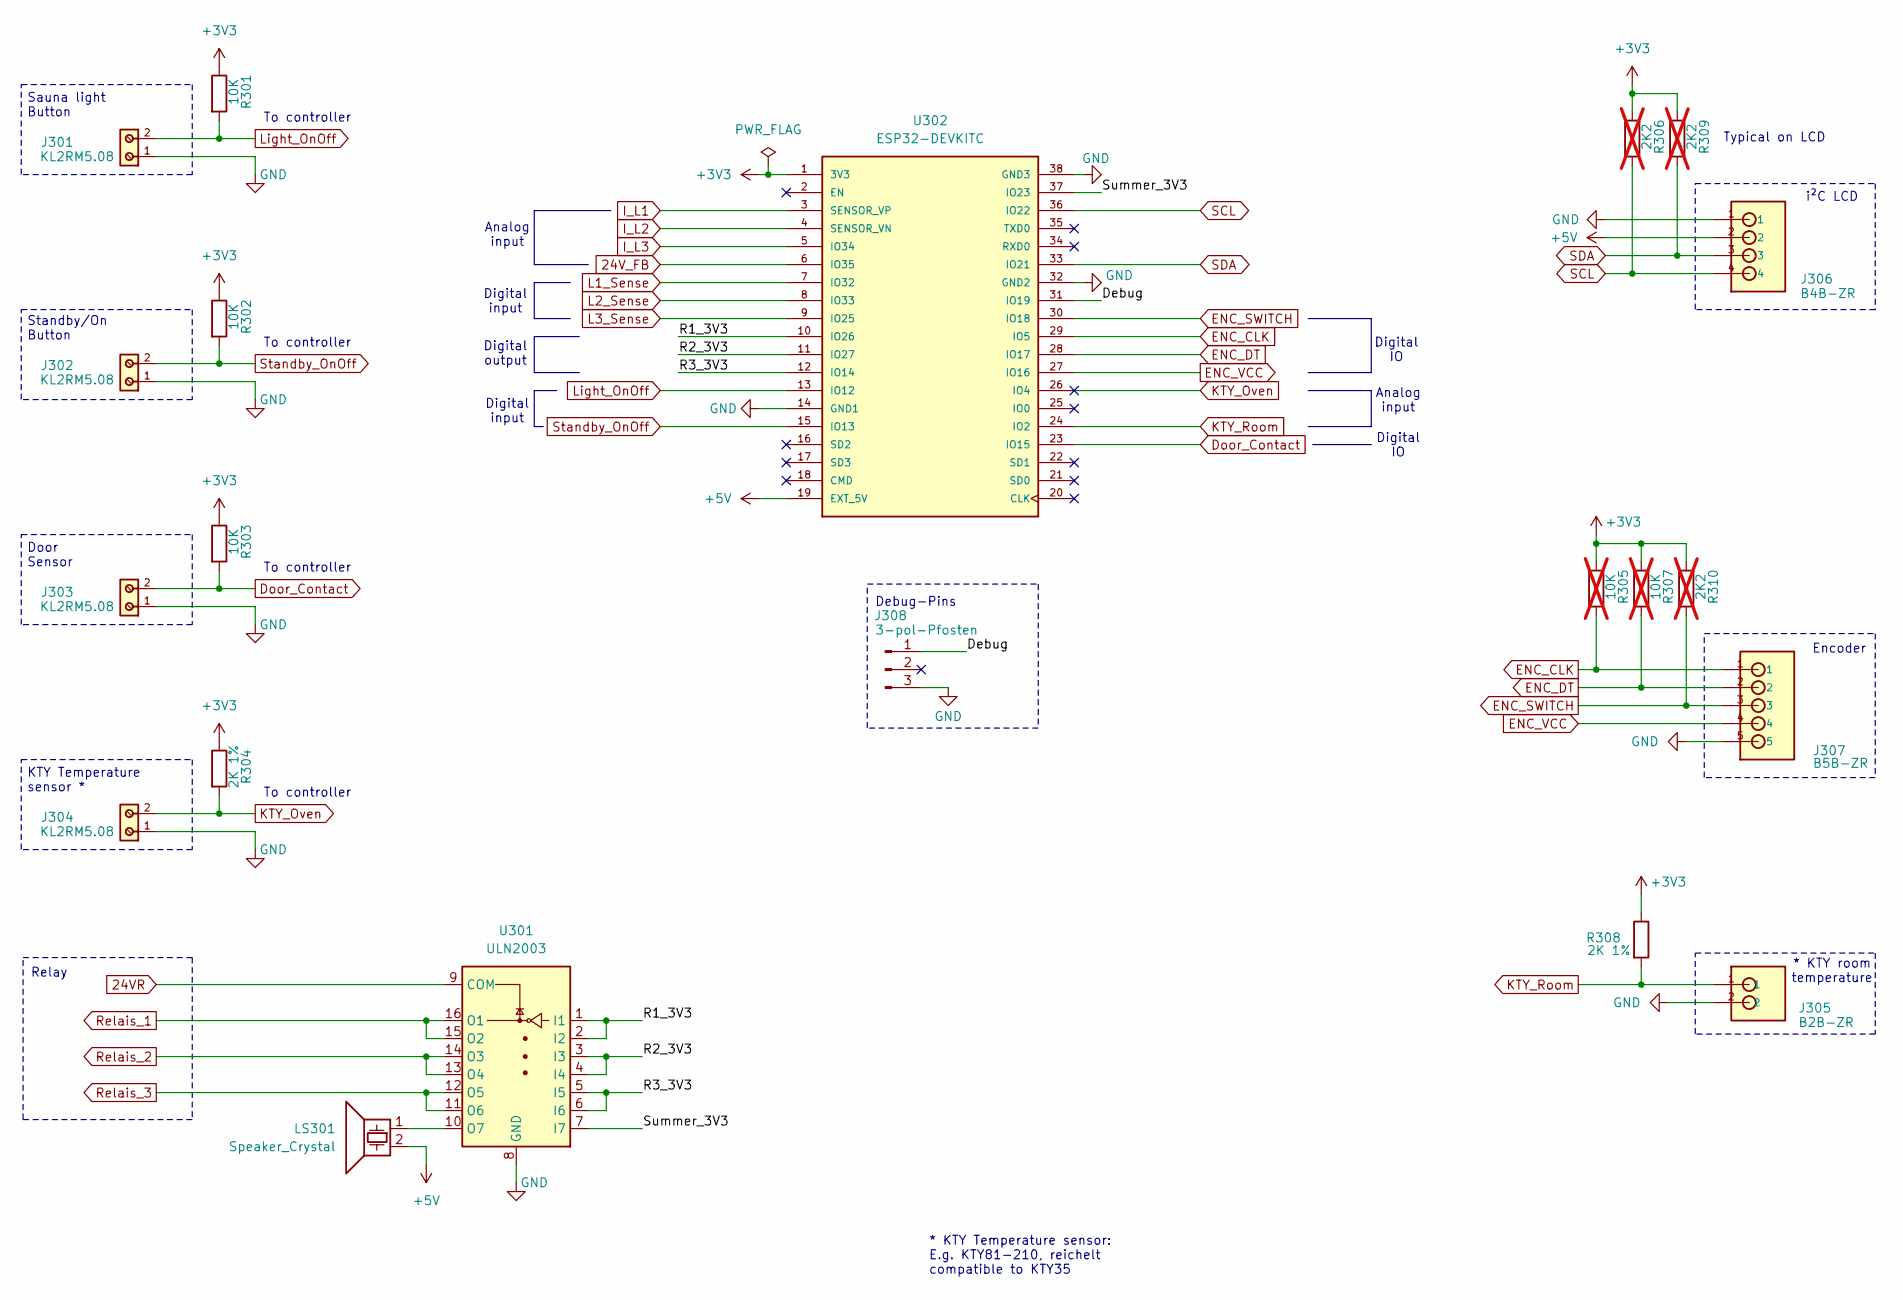
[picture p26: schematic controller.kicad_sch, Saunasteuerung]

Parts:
J301, J302, J303, J304: KL2RM5.08; Terminal_Block_2_RM5.08
J305: B2B-ZR
J306: B4B-ZR
J307: B5B-ZR
J308: 3-pol-Pfosten; PinHeader_1x03_P1.00mm_Vertical
LS301: Speaker_Crystal; Buzzer_TDK_PS1240P02BT_D12.2mm_H6.5mm
R301, R302, R303: 10K; R_1206_3216Metric
R304, R308: 2K 1%; R_1206_3216Metric
R305, R307: 10K; R_1206_3216Metric; not fitted
R306, R309, R310: 2K2; R_1206_3216Metric; not fitted
U301: ULN2003; DIP-16_W7.62mm
U302: ESP32-DEVKITC; ESP32_DevKit_V4; PARTREV N/A

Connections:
24VR: U301.9 (COM); also elsewhere on the board
24V_FB: U302.6 (IO35); also elsewhere on the board
+3V3: R301.1, R302.1, R303.1, R304.1, R305.1, R306.1, R307.1, R308.1, R309.1, R310.1, U302.1 (3V3); also elsewhere on the board
+5V: J306.2, LS301.2, U302.19 (EXT_5V); also elsewhere on the board
/Controller part/Debug: J308.1, U302.31 (IO19)
/Controller part/R1_3V3: U301.1 (I1), U301.2 (I2), U302.10 (IO26)
/Controller part/R2_3V3: U301.3 (I3), U301.4 (I4), U302.11 (IO27)
/Controller part/R3_3V3: U301.5 (I5), U301.6 (I6), U302.12 (IO14)
/Controller part/Summer_3V3: U301.7 (I7), U302.37 (IO23)
Door_Contact: J303.2, R303.2, U302.23 (IO15)
ENC_CLK: J307.1, R305.2, U302.29 (IO5)
ENC_DT: J307.2, R307.2, U302.28 (IO17)
ENC_SWITCH: J307.3, R310.2, U302.30 (IO18)
ENC_VCC: J307.4, U302.27 (IO16)
GND: J301.1, J302.1, J303.1, J304.1, J305.2, J306.1, J307.5, J308.3, U301.8 (GND), U302.14 (GND1), U302.32 (GND2), U302.38 (GND3); also elsewhere on the board
I_L1: U302.3 (SENSOR_VP); also elsewhere on the board
I_L2: U302.4 (SENSOR_VN); also elsewhere on the board
I_L3: U302.5 (IO34); also elsewhere on the board
KTY_Oven: J304.2, R304.2, U302.26 (IO4)
KTY_Room: J305.1, R308.2, U302.24 (IO2)
L1_Sense: U302.7 (IO32); also elsewhere on the board
L2_Sense: U302.8 (IO33); also elsewhere on the board
L3_Sense: U302.9 (IO25); also elsewhere on the board
Light_OnOff: J301.2, R301.2, U302.13 (IO12)
unnamed: LS301.1, U301.10 (O7)
Relais_1: U301.15 (O2), U301.16 (O1); also elsewhere on the board
Relais_2: U301.13 (O4), U301.14 (O3); also elsewhere on the board
Relais_3: U301.11 (O6), U301.12 (O5); also elsewhere on the board
SCL: J306.4, R306.2, U302.36 (IO22)
SDA: J306.3, R309.2, U302.33 (IO21)
Standby_OnOff: J302.2, R302.2, U302.15 (IO13)

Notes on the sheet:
Typical on LCD
i²C LCD
Digital input
* KTY Temperature sensor: E.g. KTY81-210, reichelt compatible to KTY35
Analog input
Standby/On Button
Debug-Pins
To controller
Encoder
Digital output
Sauna light Button
Digital IO
Relay
KTY Temperature sensor *
Door Sensor
* KTY room temperature

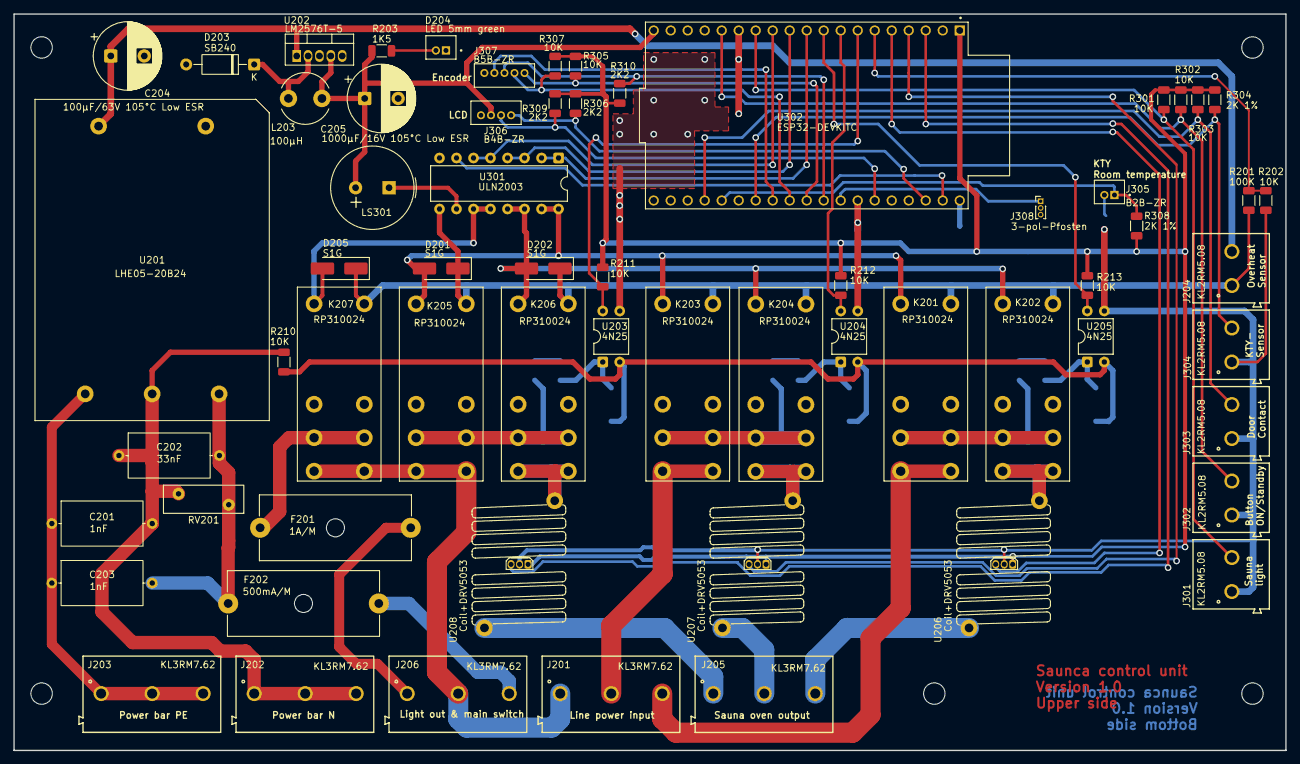
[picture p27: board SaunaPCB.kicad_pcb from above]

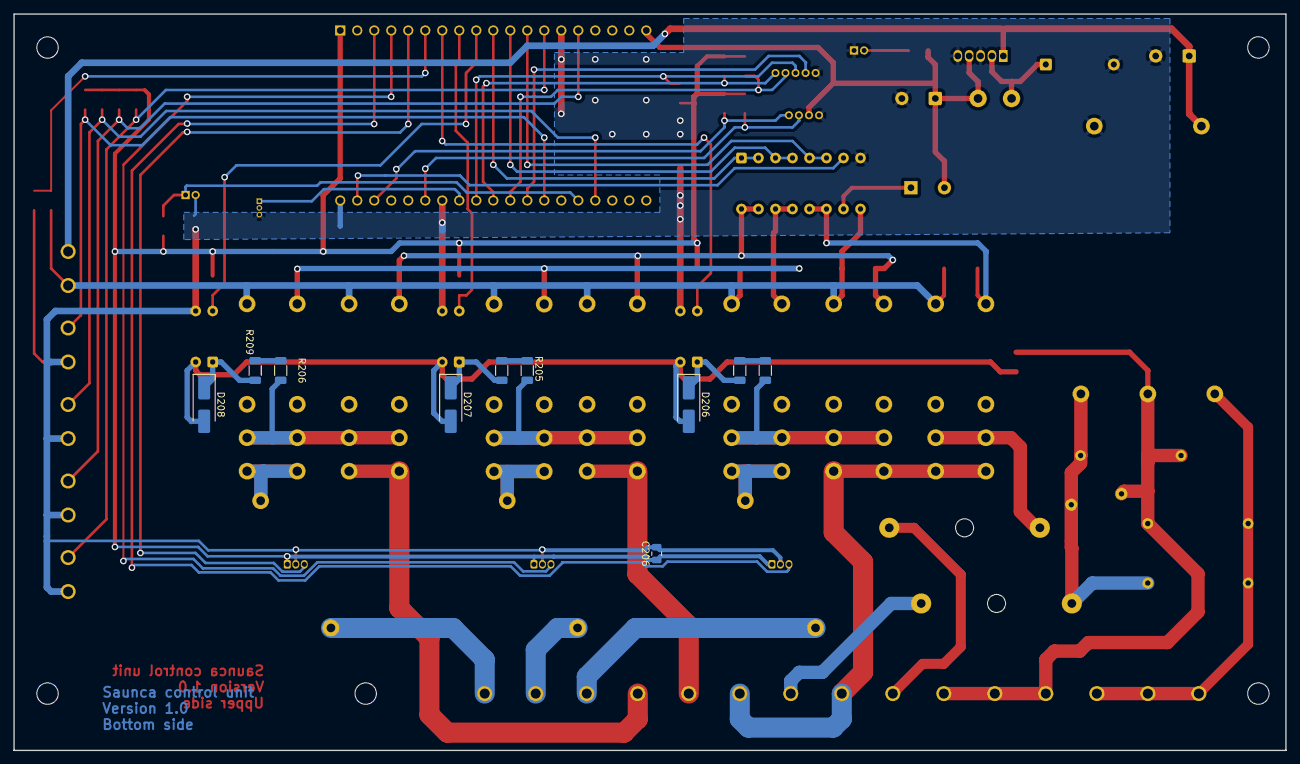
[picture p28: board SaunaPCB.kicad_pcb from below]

Board: 2 copper layers, 190.0 x 110.0 mm, 78 parts (10 on the bottom side), 59 nets.

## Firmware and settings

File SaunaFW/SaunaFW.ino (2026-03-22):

#include <WiFi.h>
#include <NTPClient.h>
#include <WiFiUdp.h>
#include <Wire.h>
#include <LiquidCrystal_I2C.h>
#include <ESP32RotaryEncoder.h>
#include "globals.h"

// ----------------------------------------------------------------------------
// My SaunaFW main module(s)
// contains Arduino setup and loop functions
// Board select: ESP32C3 Dev Module
// ----------------------------------------------------------------------------

//#define CHK_WATERMARK_ON          // if defined watermark (stack) check enabled

// ----------------------------------------------------------------------------
// String area
// ----------------------------------------------------------------------------
const char HelloStr[]     = "Sauna Control V1.0.0 (FreeRTOS)";
const char SetupFinish[]  = "Setup finished.";

// ----------------------------------------------------------------------------
// define task handles, used for communication with the tasks
// ----------------------------------------------------------------------------
TaskHandle_t KTY_TskHandle;       // KTY measurment task 
TaskHandle_t IODrvive_TskHandle;  // IO Drive task
TaskHandle_t Relay1_TskHandle;    // Task for relay 1
TaskHandle_t Relay2_TskHandle;    // ditto relay 2
TaskHandle_t Relay3_TskHandle;    // ditto relay 3
TaskHandle_t Wifi_TskHandle;      // Wifi task
TaskHandle_t WM_TskHandle;        // Stack measurement task

// ----------------------------------------------------------------------------
// Sub functions of setup and loop
// ----------------------------------------------------------------------------
void HandleConfiguration(void)
{
  MyConfig_ReadConfig();                    // initial eprom read
  while (EE_Valid != ConfigState)           // if not OK...
  {
    MyConfig_PerformConfigDialog();         // enter config dialog
    MyConfig_ReadConfig();                  // read eeprom againg
  }                                         // until content is valid
  //MyConfig_PerformConfigDialog();         // for testing
  TargetTemperature = DEF_TEMPERATURE;      // set actual = default value
  myEnc.setEncoderValue(TargetTemperature); // also in encoder module
}

// ----------------------------------------------------------------------------
// Check task to control stack requirement for ever task
// only temporarely used to determine the required stack size for ervery task
// control by #define at the beginning of this module
// ----------------------------------------------------------------------------
void printWatermark(void *pvParameters)
{
    while(1)
    {
        delay(2000);
        SP(pcTaskGetName(KTY_TskHandle));      SP(", STACK: "); SPLF(uxTaskGetStackHighWaterMark(KTY_TskHandle));
        SP(pcTaskGetName(IODrvive_TskHandle)); SP(", STACK: "); SPLF(uxTaskGetStackHighWaterMark(IODrvive_TskHandle));
        SP(pcTaskGetName(Relay1_TskHandle));   SP(", STACK: "); SPLF(uxTaskGetStackHighWaterMark(Relay1_TskHandle));
        SP(pcTaskGetName(Relay2_TskHandle));   SP(", STACK: "); SPLF(uxTaskGetStackHighWaterMark(Relay2_TskHandle));
        SP(pcTaskGetName(Relay3_TskHandle));   SP(", STACK: "); SPLF(uxTaskGetStackHighWaterMark(Relay3_TskHandle));
      //SP(pcTaskGetName(Wifi_TskHandle));     SP(", STACK: "); SPLF(uxTaskGetStackHighWaterMark(Wifi_TskHandle));
        SPLF("");
    }
}

// ----------------------------------------------------------------------------
// Start all necessary tasks and assign task handler
// ----------------------------------------------------------------------------
void StartAllTasks(void)
{
            //fct name        descr. name,  Stack parameter priority handle
  xTaskCreate(MyKTY_Task,     "KTY calc",   1500, NULL,     1,       &KTY_TskHandle);
  xTaskCreate(MyIODrive_Task, "IODrive",    1000, NULL,     1,       &IODrvive_TskHandle);
  xTaskCreate(MyRelay_1_Task, "Relay 1",    1200, NULL,     1,       &Relay1_TskHandle);
  xTaskCreate(MyRelay_2_Task, "Relay 2",    1200, NULL,     1,       &Relay2_TskHandle);
  xTaskCreate(MyRelay_3_Task, "Relay 3",    1200, NULL,     1,       &Relay3_TskHandle);
//  xTaskCreate(MyWiFi_Task,    "WiFi tsk",   8196, NULL,     1,       &Wifi_TskHandle);
  
  #ifdef CHK_WATERMARK_ON
    xTaskCreate(printWatermark, "Watermark",  2048, NULL,     1,       &WM_TskHandle);
  #endif  
}

// ----------------------------------------------------------------------------
void setup() 
{
  Serial.begin(115200); 	
  MyEncoderSetup();             // setup rotary encoder  
  delay(1000);                  // establish serial monitor
  Serial.println(HelloStr);     // first hello on serial console
  HandleConfiguration();        // read configuration, start configurator if necessary
  StartAllTasks();              // start all tasks
  Serial.println(SetupFinish);  // end of arduino setup function; enter main loop



  //MyGUI_Init();                 // init all GUI related topics
  //MyRelays_Init();              // switch all off
  //MySystem_Init();              // init HW timer module
  //MyIODrive_Init();             // init debouncer and edge handler
  //MyKTY_Init();                 // prepare KTY analogue measurment
 
  //MyWifiHandler_Init();         // Connect WiFi 
  //MyNTPHandler_Init();          // Establish NTP serive WLAN connected and NTP enabled
  //MySystem_StartTimer();        // OS HW Timer start
  //MyGUI_Prepare_LCD();          // write constant text to LCD
  
}

// ----------------------------------------------------------------------------
void loop() 
{
    // At this moment test code only

  /*
  if(flag_TargetTemperatureChanged)
  {
    Serial.println(TargetTemperature);
    flag_TargetTemperatureChanged = false;
  }
  // WERTE STIMMEN NOCH NICHT

  if(flag_NewTemperatureAvailable)
  {
    Serial.print("Room:  "); Serial.println(RoomTemperature);
    Serial.print("Sauna: "); Serial.println(SaunaTemperature);
    flag_NewTemperatureAvailable = false;
  }
      delay(500);
      if (flag_mode_pressed)    Serial.println ("Mode pressed");
      if (flag_mode_released)   Serial.println ("Mode released"); 
      if (flag_light_pressed)   Serial.println ("Light pressed");
      if (flag_light_released)  Serial.println ("Light released");
      if (flag_door_closed)     Serial.println ("Door closed");
      if (flag_door_opened)     Serial.println ("Door opened");    

  */
  
    delay(500);

    if (flag_mode_pressed && REL_1_IS_OFF)  {MyRelays_Function(Cmd_Relay1_On); Serial.println("Switch relay 1 on");}
    if (flag_mode_pressed && REL_1_IS_ON)   {MyRelays_Function(Cmd_Relay1_Off);Serial.println("Switch relay 1 off");}

    if (flag_light_pressed && REL_3_IS_OFF)  {MyRelays_Function(Cmd_Relay3_On); Serial.println("Switch relay 3 on");}
    if (flag_light_pressed && REL_3_IS_ON)   {MyRelays_Function(Cmd_Relay3_Off);Serial.println("Switch relay 3 off");}
  

      MyIODrive_ClearEdges();
}
  
// ----------------------------------------------------------------------------
//  end of main module
// ----------------------------------------------------------------------------

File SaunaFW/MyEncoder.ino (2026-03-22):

// ----------------------------------------------------------------------------
// My SaunaFW Encoder module 
// contains all encoder related functions 
// Board select: ESP32C3 Dev Module
// This module is NOT an FreeRTOS Task. It is a completely ISR driven module
//
// ----------------------------------------------------------------------------

// ----------------------------------------------------------------------------
// Encoder call back function for the rotary encoder turn
void MyEncoderKnobCallback( long value )
{
  TargetTemperature = (unsigned int) value;   	// set new target temperature
  flag_TargetTemperatureChanged = true;       	// set flag for main
}

// ----------------------------------------------------------------------------
// Encoder call back function for the rotary push button
void MyEncoderButtonCallback( unsigned long duration )
{
  if (duration > Temp_Store)                  	// detect long press
  {
    DEF_TEMPERATURE = TargetTemperature;   			// actual target => default
    flag_DefaultTemperatureChanged = true;    	// set flag for main
  }
}

// ----------------------------------------------------------------------------
void MyEncoderSetup() 
{
	// This tells the library that the encoder has its own pull-up resistors
	myEnc.setEncoderType( EncoderType::HAS_PULLUP );

	// Range of values to be returned by the encoder: minimum is 1, maximum is 10
	// The third argument specifies whether turning past the minimum/maximum will
	// wrap around to the other side:
	//  - true  = turn past 10, wrap to 1; turn past 1, wrap to 10
	//  - false = turn past 10, stay on 10; turn past 1, stay on 1
	myEnc.setBoundaries( Temp_Min, Temp_Max, false );

	// The function specified here will be called every time the knob is turned
	// and the current value will be passed to it
	myEnc.onTurned( &MyEncoderKnobCallback );
	
  // The function specified here will be called every time the button is pushed and
	// the duration (in milliseconds) that the button was down will be passed to it
	myEnc.onPressed( &MyEncoderButtonCallback );

	// This is where the inputs are configured and the interrupts get attached
	myEnc.begin();
}

// ----------------------------------------------------------------------------
//  end of the encoder control module
// ----------------------------------------------------------------------------

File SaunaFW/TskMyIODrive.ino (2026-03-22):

// ----------------------------------------------------------------------------
// My Sauna control IO Drive module 
// Performs these actions:
// read in and debounce all digital inputs (buttons, door contact)
// generate edge signals from input events
//
// Please consider: Evan digital input are often swichted to ground the
// module uses POSITIVE LOGIC!
// ----------------------------------------------------------------------------

#define PIN_MODE_PRESSED    (false == digitalRead(INP_MODE))
#define PIN_LIGHT_PRESSED   (false == digitalRead(INP_LIGHT))
#define PIN_DOOR_CLOSED     (false == digitalRead(INP_DOOR))

uint8_t bnc_cnt = 0;		      // counter for debounce cycles (pointer to array)
uint8_t bnc_dat_array[3];	    // bouncing data input array for three samples
uint8_t deb_dat_count = 0;	  // counter for debouncer data valid decision
uint8_t bnc_dat = 0;		      // working variable for debounce algorithm
uint8_t deb_dat = 0;		      // debounced data variable
uint8_t deb_dat_old = 0;      // old variable for edge detection
bool deb_dat_valid = false;   // TRUE if debounced data is valid now

// ----------------------------------------------------------------------------
void MyIODrive_Task(void *parameter)
{
  // Init and setup task  
  uint8_t i;
  pinMode(INP_DOOR,  INPUT_PULLUP);       // pin is alwys input
  pinMode(INP_LIGHT, INPUT_PULLUP);       // pin is alwys input
  pinMode(INP_MODE,  INPUT_PULLUP);       // pin is alwys input
  for (i=0;i<3;bnc_dat_array[i++]=0);     // clear debounce array
  
  // 
  while(1)
  {
    uint8_t inputs = 0;
    // read input signals and store them in ring buffer -------------------
    if (PIN_MODE_PRESSED)   inputs = 1;   // mode in bit 0
    if (PIN_LIGHT_PRESSED)  inputs |= 2;  // light in bit 1
    if (PIN_DOOR_CLOSED)    inputs |= 4;  // door signal in bit 2
    bnc_dat_array[bnc_cnt] = inputs ;     // store in ring buffer
    
    // debounce step 1, 2, 3 ---------------------------------------------
    // set bit to "1" if not 3 times equal
    bnc_dat  = bnc_dat_array[0] ^ bnc_dat_array[1] ; // step 1
    bnc_dat |= bnc_dat_array[1] ^ bnc_dat_array[2] ; // step 2
    bnc_dat |= bnc_dat_array[2] ^ bnc_dat_array[0] ; // step 3

    // set bit to "1" if not 3 times equal --------------------------------
    deb_dat &= bnc_dat ;        				    // reset constant bits
    deb_dat |= bnc_dat_array[0] & ~bnc_dat; // set constant bits

    // handle cyclic counter ---------------------------------------------
    bnc_cnt++;
    if (3 == bnc_cnt)       // 3 = overflow
    {
      bnc_cnt = 0;          // reset cycle counter to zero
      deb_dat_valid = true; // at least one cycle is finished
    }

    // edge generation module --------------------------------------------
    if (deb_dat_valid)
    {
      if ((0 == (deb_dat_old & 1)) && (MODE_IS_PRESSED))   flag_mode_pressed   = true;
      if ((0 != (deb_dat_old & 1)) && (!MODE_IS_PRESSED))  flag_mode_released  = true; 
      if ((0 == (deb_dat_old & 2)) && (LIGHT_IS_PRESSED))  flag_light_pressed  = true;
      if ((0 != (deb_dat_old & 2)) && (!LIGHT_IS_PRESSED)) flag_light_released = true;
      if ((0 == (deb_dat_old & 4)) && (DOOR_IS_CLOSED))    flag_door_closed    = true;
      if ((0 != (deb_dat_old & 4)) && (!DOOR_IS_CLOSED))   flag_door_opened    = true;    
      deb_dat_old = deb_dat;  // update "old" variable with current values
    }

    vTaskDelay(10/portTICK_PERIOD_MS);  // 10 ms pause
  }  
}

// ----------------------------------------------------------------------------
void MyIODrive_ClearEdges(void)       // call at the end of one loop
{
    flag_mode_pressed   = false;            // reset all edge flags
    flag_mode_released  = false; 
    flag_light_pressed  = false;
    flag_light_released = false;
    flag_door_closed    = false;
    flag_door_opened    = false;
}

// ----------------------------------------------------------------------------
// end of the IO Drive (input debouncer) module
// ----------------------------------------------------------------------------

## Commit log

2026-01-24 First commit: basic file and folder set added.
    [Port_Usage_Planning.xlsx, Power_Bar.kicad_sch, Relais Powerbetrachtung.xlsx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]
2026-01-25 Data home brew current sensor added
2026-01-25 Working on schematic and PCB -AC/DC and DC/DC converters with correct symbol and footprint now - rough placement of the power parts
    [Power_Bar.kicad_sch, RSH2-2405S_H3-R.step, SaunaPCB.kicad_pcb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]
2026-01-26 Work on documnets and net classes
    [Power_Bar.kicad_sch, SaunaPCB.kicad_pcb]
2026-01-27 PCB Planning.docx added
2026-01-30 Rework trace width calculation Distances (legal requirements) added
2026-01-30 Working on PCB placment optimisation Trace width and distance
    [Power_Bar.kicad_sch, SaunaPCB.kicad_pcb]
2026-01-31 Still working on placement and routing
    [Power_Bar.kicad_sch, SaunaPCB.kicad_pcb]
2026-01-31 Relay power supply changed
    [Power_Bar.kicad_sch, SaunaPCB.kicad_pcb, controller.kicad_sch]
2026-02-01 Working on schematic: - Own ESP32 Devkit V4 device used. - ESP32 connections added (all signals from page on connected)
    - Next steps: Connection to LCD, Relay driver, Encoder Interface and standby LED
    [Port_Usage_Planning.xlsx, Power_Bar.kicad_sch, SaunaPCB.kicad_pcb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]
2026-02-01 Minor changes on port usage
    [Port_Usage_Planning.xlsx, controller.kicad_sch]
2026-02-03 5V regulator changed
    [KL2_RM_5.08_691216410002 (rev1).stp, KL2_RM_7.62_691210910002 (rev1).stp, KL3_RM_5.08_691216410003 (rev1).stp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]
2026-02-04 some step files added
    [Power_Bar.kicad_sch, SaunaPCB.kicad_pcb, controller.kicad_sch]
2026-02-05 Hall sensors for current measurement added
    [Power_Bar.kicad_sch, SaunaPCB.kicad_pcb, controller.kicad_sch]
2026-02-06 Datasheet hall sensors added, folder structure changed
2026-02-06 Hall effect sensor type changed to DRV5053 .gitignore added: ignore .zip files in KiCAD backup folder
    [Power_Bar.kicad_sch]
2026-02-06 First routing almost finished Connector to LCD and encoder to be added!
    [Power_Bar.kicad_sch, SaunaPCB.kicad_pcb]
2026-02-06 Connector to LCD and decoder added
    [SaunaPCB.kicad_pcb, controller.kicad_sch]
2026-02-07 Usage ULN changed Top silkscreen PCB almost ready Values Diodes changed all 1N4004 => SG1 Relay diodes changed from NB to used (for security reasons; Diode in ULN may be not powerful enough)
    [Power_Bar.kicad_sch, SaunaPCB.kicad_pcb, controller.kicad_sch]
2026-02-07 Firmware coding started. LCD and encoder running
    todos
    - encoder change from polling to interrupt usage
    - switch input connected to interrupt input
    [Port_Usage_Planning.xlsx]
2026-02-08 ^MOV and Fuse added
    [Power_Bar.kicad_sch, SaunaPCB.kicad_pcb, controller.kicad_sch]
2026-02-08 Power LED changed to JST connector KTY room added
    [Power_Bar.kicad_sch, SaunaPCB.kicad_pcb, controller.kicad_sch]
2026-02-08 Update port planning Documents/Manual_K2_(simple_control_unit).pdf
    - VCC encoder from controller now
    - KTY room added
    - buzzer added
    [Port_Usage_Planning.xlsx]
2026-02-08 Standard encoder library replaced by ESP specific library. Full interrupt driven. New module to bundle all encoder specific integration
    Test code for new libary in loop.
    [SaunaFW.ino, globals.h]
2026-02-08 Working on the SW:
    - Hardware timer 1ms running
    - Scheduler 1/5 ms running
    - Relay and Application module with stubs (no function yet)
2026-02-08 Coding of relay FSM finished. Code can be compiled but is not tested!
2026-02-09 Plot folder with plot files added.
    [SaunaPCB-B_Cu.gbr, SaunaPCB-B_Mask.gbr, SaunaPCB-B_Paste.gbr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]
2026-02-09 Module for KTY added direct from KI, not adjusted at current structure.
2026-02-10 Unknown changes from BEKO laptop
    [SaunaPCB.kicad_pcb]
2026-02-11 Home brew sensor: Coil and hall sensor combined to one unit to avoid overlap errors on DRC DRC errors removed; 2 warnings left => both acceptable.
    [Power_Bar.kicad_sch, SaunaPCB.kicad_pcb]
2026-02-12 Backlight signal removed two debug pins added remarks regarding KTY added
    [Port_Usage_Planning.xlsx, SaunaPCB.kicad_pcb, controller.kicad_sch]
2026-02-12 Input debouncer and edge generator are working now. Next step: connect light button with relay 3 FSM to test the FSM.
2026-02-13 Working on relay function. Code can not be compiled in this version.
2026-02-13 - Relay module reworked. Now ready & tested. - Light handler to Task51 added to handle light button in the background. - Error in SW timer removed - Run time task 51 performed (less 3µs!)
    Functions described above are working fine and as expected
    [globals.h]
2026-02-14 Temperature functions implemented:
    - KTY module implemented in scheduling
    - Two channels to be calculated
    - change flags are generated
    Code can be compiled (run time about 100µs), but is not tested yet!
2026-02-14 Working on KTY module. => Module gives temperature values, but not plausible
    maybe a sensor issue, to be checked.
    Test code for KTY moved to text file.
    [globals.h]
2026-02-22 Room KTY moved to IO0 (prior buzzer) Buzzer moved to IO23 (prior Debung_2) Debug_2 removed
    Reason IO0 does not work properly as ADC input.
    Pretty low input impediance...
    [SaunaPCB.kicad_pcb, controller.kicad_sch]
2026-03-19 Document folder update: - chaned IO Port_Usage_Planning.xls - new information regarding KTY81 - textfile with usefuls links
    [Port_Usage_Planning.xlsx]
2026-03-22 Software changed from cooperative multi tasking to preemptive multi tasking based on the ESP32 FreeRTOS
    The following tasks are coded and running and roughly tested as OK:
    -------------------------------------------------------------------
    - Relay_x tasks are running, tested, OK
    - IODrive task is running; , tested, OK
    - High watermark (=stack) check task is running, tested OK
    These tasks are not OK and must be debugged / fixed:
    ----------------------------------------------------
    - KTY task is running; results are wrong
    - Wifi task leads to kernal panic (disabled at this moment)
    [MyConfig.ino, MyEncoder.ino, SaunaFW.ino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]
2026-03-22 Remarks to port usage added
    [Port_Usage_Planning.xlsx]
2026-03-22 Simulator circuit to give different temperatures. Useful for test of KTY measurement and debug the regulation algorithm.
    [KTYSimulator.kicad_pcb, KTYSimulator.kicad_sch]
